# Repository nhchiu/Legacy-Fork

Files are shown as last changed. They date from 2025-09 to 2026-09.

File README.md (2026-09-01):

# Legacy Fork

*It's not only a fork of [Voron Legacy](https://github.com/VoronDesign/Voron-Legacy), but also a big "fork" (a.k.a. [Voron Trident](https://github.com/VoronDesign/Voron-Trident)).*

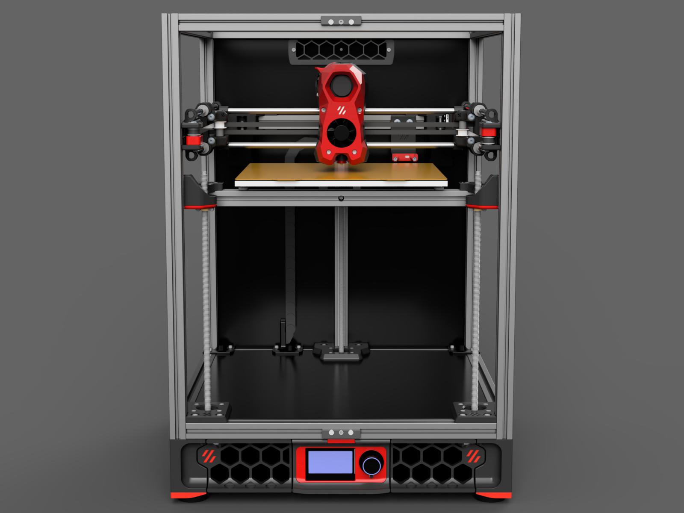
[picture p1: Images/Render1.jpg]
Render1


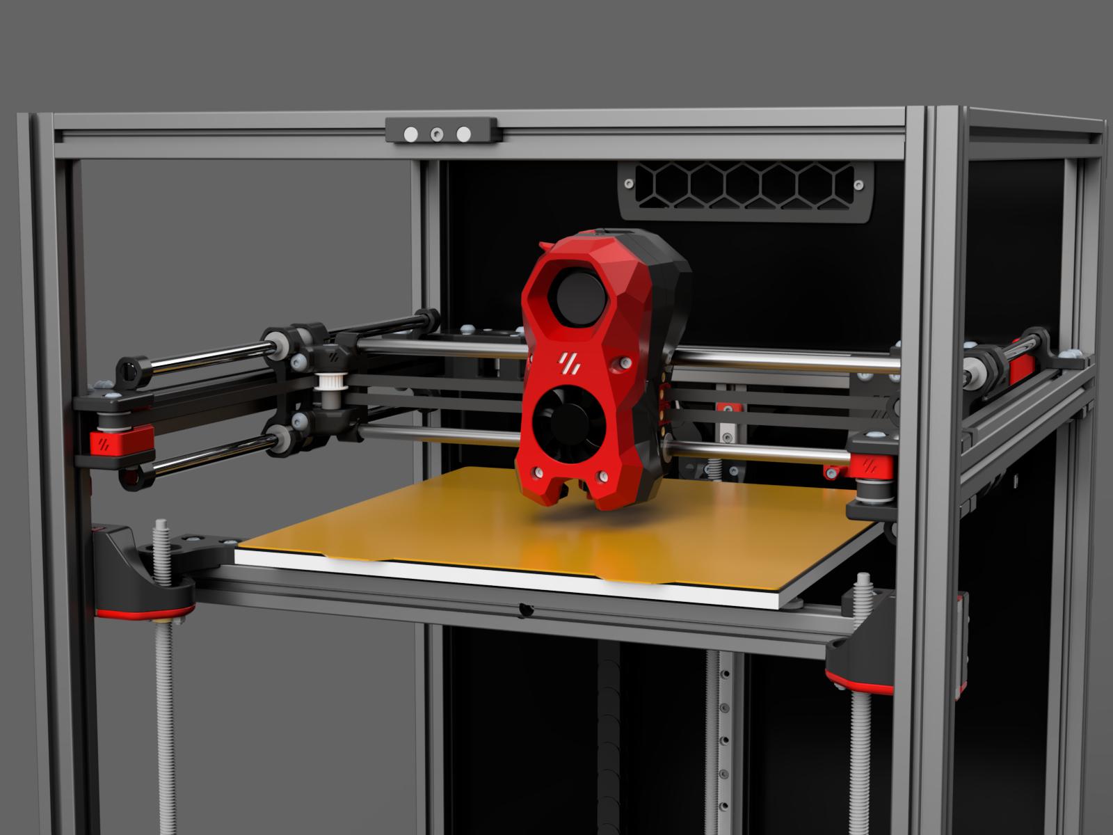
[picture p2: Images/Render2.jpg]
Render2


## Features

- Print size: 250mm x 250mm x 250mm.
- Trident 250 with Legacy style gantry.
- [Stealthburner](https://github.com/VoronDesign/Voron-Stealthburner) or [A4T](https://github.com/Armchair-Heavy-Industries/A4T) toolhead, umbilical wire management (no drag chains).
- KlickyNG for Z tilt and bed mesh.

This printer is not design for everyone.
It's just a slightly more "modernized" version of Legacy (also slightly larger print area).
If you're looking for a good reliable printer, build a Trident.

Here's a simple comparison to help you decide:

| | Legacy | Legacy Fork | Trident |
| --- | --- | --- | --- |
| Frame Size (W\*D\*H) | 410 \* 410 \* 410 | 410 \* 410 \* 500 | 410 \* 410 \* 500 |
| Print Area (X\*Y\*Z) | 230 \* 230 \* 240 | **250 \* 250 \* 250**  | **250 \* 250 \* 250** |
| Enclosure | No | **Yes** | **Yes** |
| Expected Speed/Accel | Lower | Lower | **Higher** |
| Motion system | 10 rods | 6 rods(XY), 3 rails(z) | 6 rails |

## BOM

[BOM.md](./BOM.md)

## Recommended Mods

- [PUG (Parametric umbilical gland)](https://www.printables.com/model/378567-pug-parametric-umbilical-gland)
- [Trident Inverted Electronics Bay Mod](https://github.com/VoronDesign/VoronUsers/tree/main/printer_mods/LoganFraser/TridentInvertedElectronics)
- [Print-in-place Panel Latch](https://www.printables.com/model/1042802-sturdy-print-in-place-panel-latch-for-2020-extrusi)
- [Foldable Spool holder](https://www.printables.com/model/1233299-tri-direction-foldable-spool-holder)
- [Sturdy handler](https://www.printables.com/model/793387-voron-24r2trident-sturdy-handler-remix)

## Credits

- [Voron Design](https://vorondesign.com/) team for Trident, Legacy, and Stealthburner.
- [Klicky(NG) Probe](https://github.com/jlas1/Klicky-Probe).
- [Voron Construct](https://github.com/PrintersForAnts/Voron-Construct) for handy CAD models.
- [Prusawire](https://www.printables.com/model/1363547-prusawire-2025b1-beta-1) for the belt tensioner design.
- [ApexClips](https://github.com/ApexArray/ApexClips).

> [!TIP]
> Support my work on the following platforms. Thank you!
>
> 
> 

## Changelog

### 2026 / 09 / 01

- AB drive mounts
  - Shift the assembly 2mm towards the front to fit rear panel with 1mm foam. *(untested)*
- X carriage
  - Added a variant for inductive probe (OMRON TL-Q5MC2). *(untested)*
- XY joints
  - Adjusted to fit the other changes.

### 2026 / 08 / 21

- Port Trident R2 upgrades:
  - Uses Trident R2 Z assembly.
  - New AB drive mounts:
    - Shorter belt path. (requires **4 more F695 bearings**)
    - Steppers mount with all 4 screws.
    - Cutouts for wires to pass through.
    - ~Requires **3mm foam on the rear panel**.~
- Clamping mechanism on X rod holders.
- Shifted the print area towards the front so it uses stock Trident Z carriages / bed mounts.

### 2025 / 10 / 21

Use hex nuts instead of heatset inserts to hold the X axis onto XY joints.

### 2025 / 10 / 02

New belt clip and tensioner design.

- Belt tensioner design inspired by [Prusawire](https://www.printables.com/model/1363547-prusawire-2025b1-beta-1).
- [ApexClips](https://github.com/ApexArray/ApexClips)
- Now the front idlers are fixed position.

### 2025 / 09 / 10

Initial release.

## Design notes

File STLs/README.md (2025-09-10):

The STLs regarding the following sub-assemblies are not included:

- Toolhead
- Electronics
- Exhaust Filter
- Panels
- Skirt
- Spool Management

The default is to use parts from [the Trident repository](https://github.com/VoronDesign/Voron-Trident/tree/main/STLs). Most Trident mods should be compatible.

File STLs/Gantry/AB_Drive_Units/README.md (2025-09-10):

# Flipped B drive?

It means mounting the motor on the upper side of the gantry.

Pros: The belt is closer to the motor body so there's less bending torque on the motor shaft.

Cons: Depending on how you mount the umbilical wires / cable gland, the B motor might collide to the back of the toolhead when homing.
One way to get around it is to home X axis before homing Y. There should be enough over-travel so it won't collide in the print area.

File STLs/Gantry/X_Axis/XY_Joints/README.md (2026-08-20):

Put one of the `Printed_Shim_0.7mm` at both sides of the 20T idlers if you're using generic/POWGE ones (about 8.5mm width), so the total width adds up to 10mm.

Check the width of your idler to see if you need it (e.g. Gates idler).

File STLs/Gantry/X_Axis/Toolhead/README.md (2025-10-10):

# Toolhead

- [Voron Stealthburner](https://github.com/VoronDesign/Voron-Stealthburner/tree/main/STLs)
- [A4T](https://github.com/Armchair-Heavy-Industries/A4T) (CW2 carriage)

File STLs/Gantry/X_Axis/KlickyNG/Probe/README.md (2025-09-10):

Get the STLs from here: [https://github.com/jlas1/Klicky-Probe/blob/main/Probes/KlickyNG/STL/KlickyNG_Probe.zip](https://github.com/jlas1/Klicky-Probe/blob/main/Probes/KlickyNG/STL/KlickyNG_Probe.zip).

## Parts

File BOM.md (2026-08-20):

# BOM

This is a very brief BOM. Only core components are listed here.
Refer to CAD, Trident and Legacy BOM for the rest.

> [!NOTE]
> \* Aliexpress links are *affiliate links*. If you purchase products through these links,
> I may earn a small commission at no additional cost to you.
> This helps support the development and maintenance of my projects.

## Trident 250 Components

| Component | Qty | Source |
| --- | --- | --- |
| Frame kit | 1 | [West3D](https://west3d.com/products/ldo-trident-frame-kit-multiple-colors) or [KB3D](https://kb-3d.com/store/frame-enclosure/471-8401-ldo-motors-frame-kit-for-voron-trident-multiple-types-1642791073246.html) |
| Panels | 1 | |
| Build plate + Heater | 1 | [West3D (LDO)](https://west3d.com/products/voron-v2-4-aluminum-build-plate-complete-kit-by-ldo-systems-heater-magnet-and-fuse-pre-applied-to-plate) |

## Fasteners

| Component | Qty | Notes | Source |
| --- | --- | --- | --- |
| M5 0.5mm Thick Shim/Washer | 20  | Optional. For alternative bearing stacks (check manual) | [Aliexpress\*](https://s.click.aliexpress.com/e/_c4MMENC7) - 5x10x0.5mm |

## Motion

| Component | Qty | Notes | Source |
| --- | --- | --- | --- |
| Linear Rods - D8mm x 320mm | 6 | | [CNA\*](https://s.click.aliexpress.com/e/_c4bX2dSv) |
| Linear Bearings - LM8LUU | 6 | | [FUSHI\*](https://s.click.aliexpress.com/e/_onqjz99)  |
| Integrated Lead Screw/Stepper Motors - 300mm | 3 | | [Siboor\*](https://s.click.aliexpress.com/e/_ombbGBv) |
| Linear Rail - MGN9H 300mm | 3 | | [CNA\*](https://s.click.aliexpress.com/e/_onEsgxV) |
| GE5C Spherical Bearing | 3 | | [FUSHI\*](https://s.click.aliexpress.com/e/_olhEbNN)  |
| GT2 20T (6mm wide) Pulley (5mm bore) | 3 | 1 is for Z endstop | [POWGE\*](https://s.click.aliexpress.com/e/_oEvDEoR)  |
| GT2 20T (6mm wide) Toothed Idler (5mm bore)  | 2 | | [POWGE\*](https://s.click.aliexpress.com/e/_olP1HSr)  |
| GT2 Open Belt LL-2GT-RF (6mm wide) | 5m  | Only need roughly 3.2m | [POWGE\*](https://s.click.aliexpress.com/e/_olP1HSr)  |
| F695 Bearing | 24  | | [FUSHI\*](https://s.click.aliexpress.com/e/_oo38KNh)  |
| NEMA17 Motors | 2 | AB motor | [Mellow\*](https://s.click.aliexpress.com/e/_om0OSnH) |

## Electronics

| Component | Qty | Notes |
| --- | --- | --- |
| Mouse Button - Micro Switch | 4 | X, Y, Z, Probe |
| SBC (Raspberry Pi alternatives) | 1 | |
| Controllers / Toolhead boards | 1 | 6 steppers in total |

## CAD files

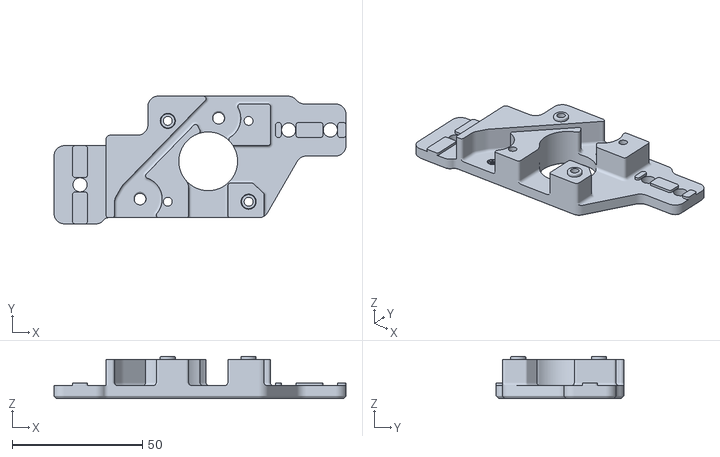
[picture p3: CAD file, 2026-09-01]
STLs/Gantry/AB_Drive_Units/B_Drive_a.stl
112.0 x 49.0 x 16.2

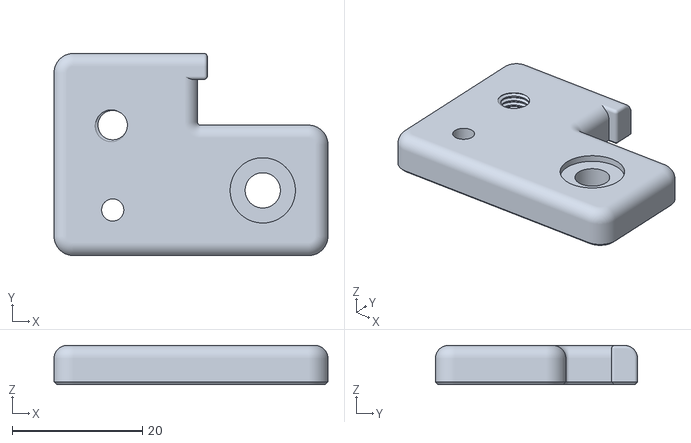
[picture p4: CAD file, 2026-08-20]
STLs/Gantry/Front_Idlers/Right_b.stl
42.0 x 31.0 x 6.00

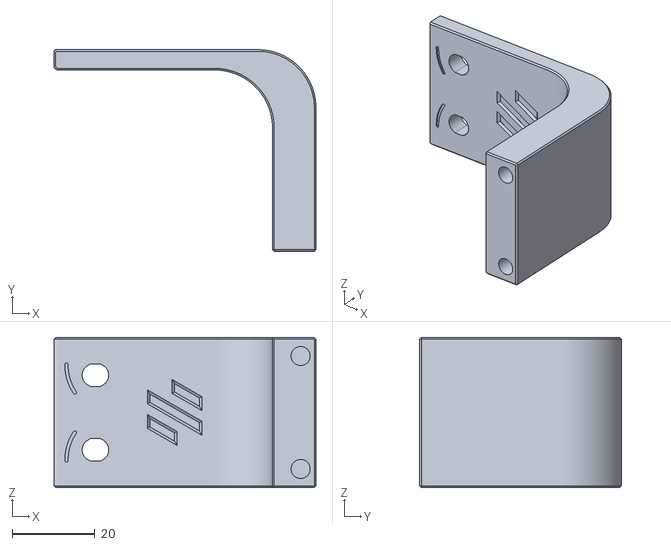
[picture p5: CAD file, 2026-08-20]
STLs/Gantry/X_Axis/KlickyNG/Dock/Dock_Mount.stl
63.2 x 48.7 x 36.3

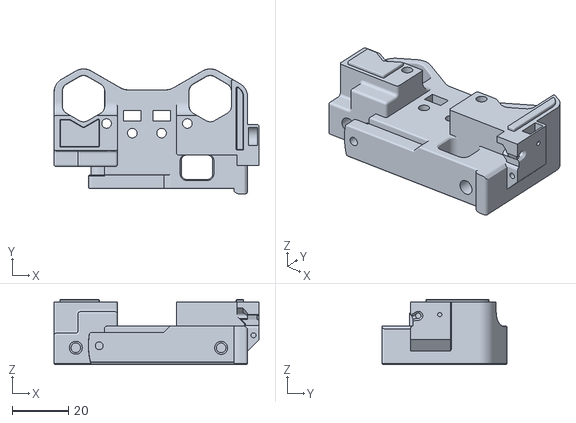
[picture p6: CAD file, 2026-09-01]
STLs/Gantry/X_Axis/X_Carriage/x_carriage_frame_left_klickyNG.stl
72.8 x 44.5 x 23.2

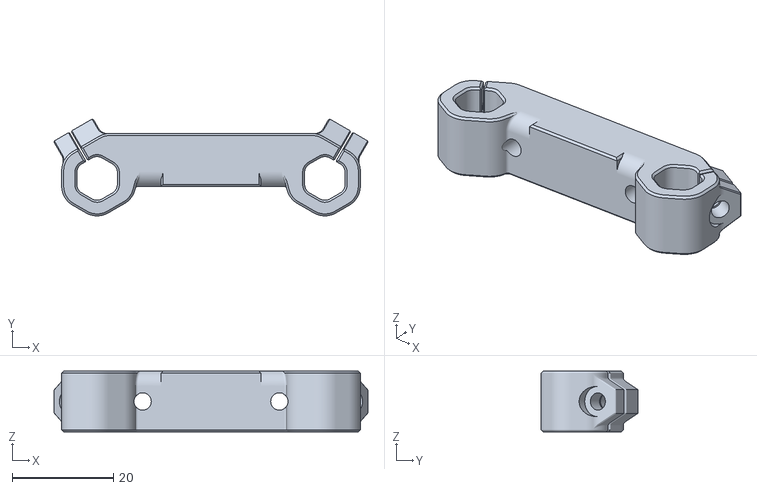
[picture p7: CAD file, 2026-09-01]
STLs/Gantry/X_Axis/XY_Joints/X_Back_Brace_x2.stl
62.0 x 19.1 x 12.0

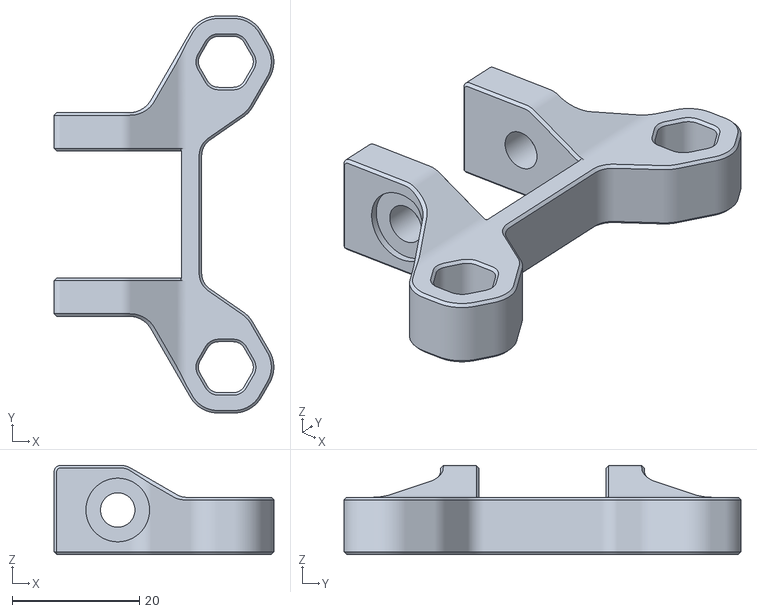
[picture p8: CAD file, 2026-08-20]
STLs/Gantry/Y_Shaft_Holder_x4.stl
34.5 x 62.4 x 14.0

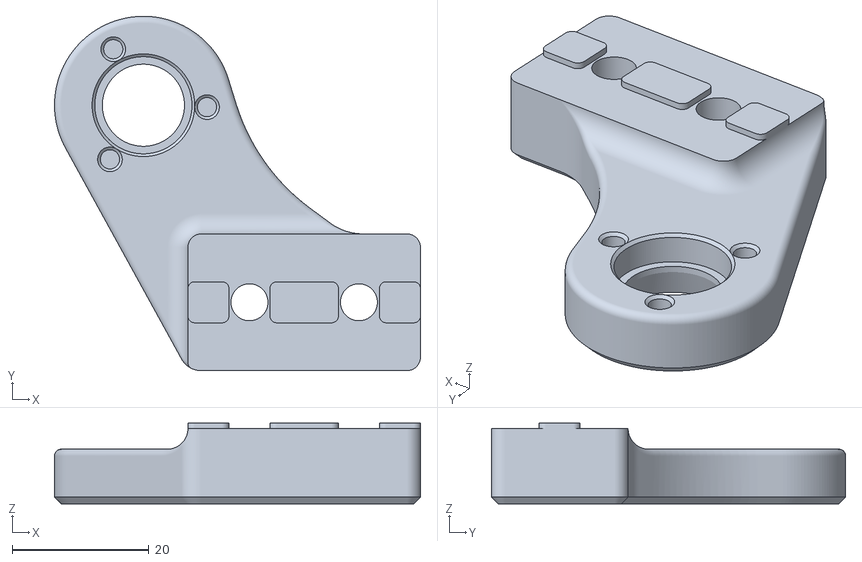
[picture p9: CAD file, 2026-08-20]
STLs/Z_Assembly/Z_Bed_Left.stl
53.5 x 51.8 x 11.8

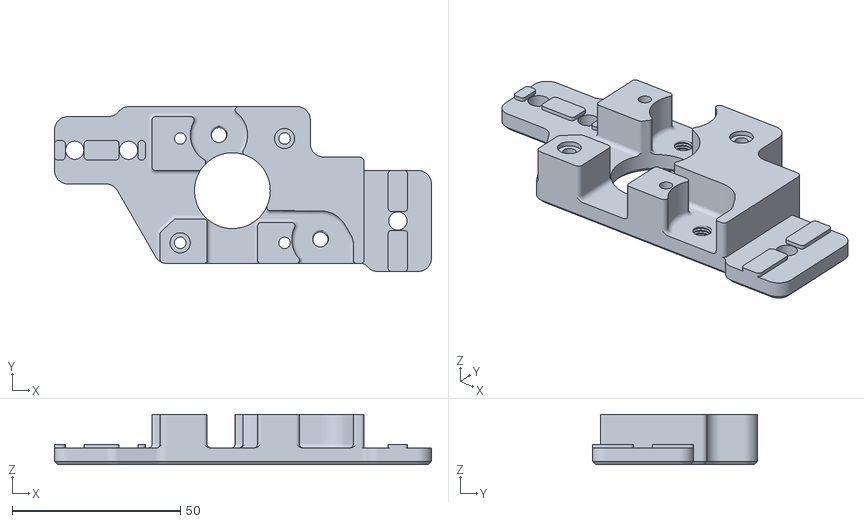
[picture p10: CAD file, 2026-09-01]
STLs/Gantry/AB_Drive_Units/A_Drive_a.stl
112.0 x 49.0 x 15.0

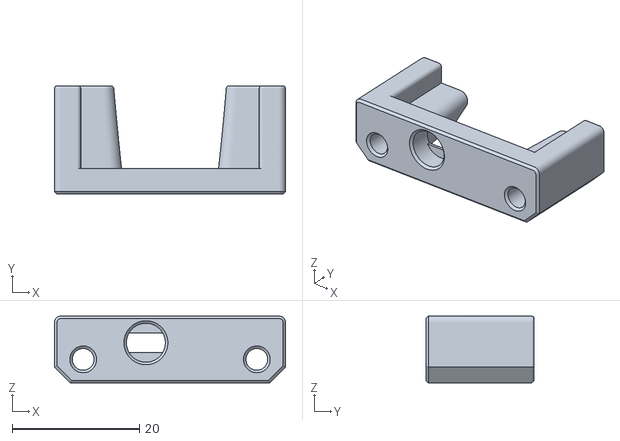
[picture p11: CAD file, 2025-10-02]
STLs/Gantry/X_Axis/KlickyNG/Dock/[a]_Probe_Dock.stl
36.3 x 17.0 x 10.5

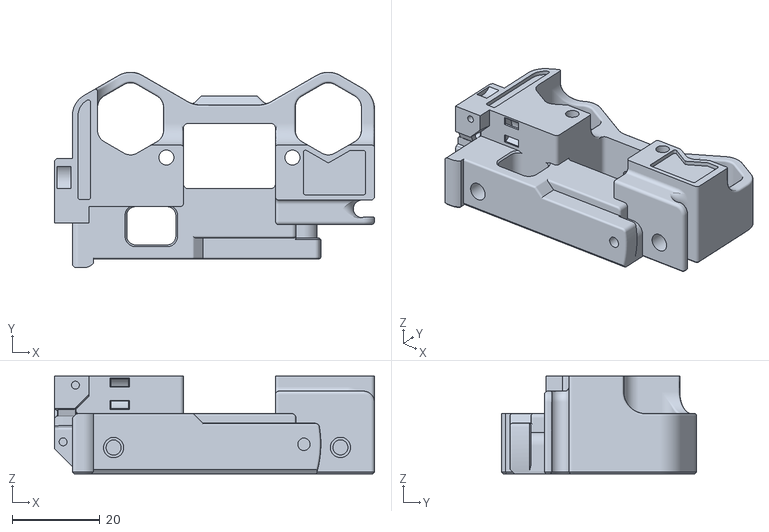
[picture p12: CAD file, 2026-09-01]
STLs/Gantry/X_Axis/X_Carriage/x_carriage_frame_right_klickyNG.stl
72.8 x 44.5 x 22.2

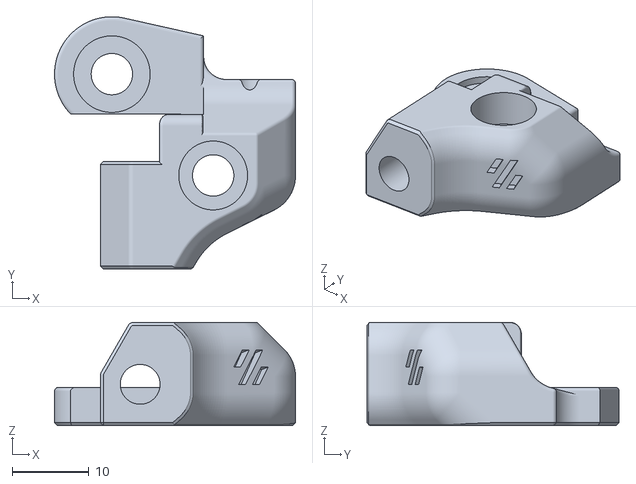
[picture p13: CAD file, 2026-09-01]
STLs/Gantry/X_Axis/XY_Joints/XY_Joint_Left_a.stl
31.5 x 33.0 x 13.5

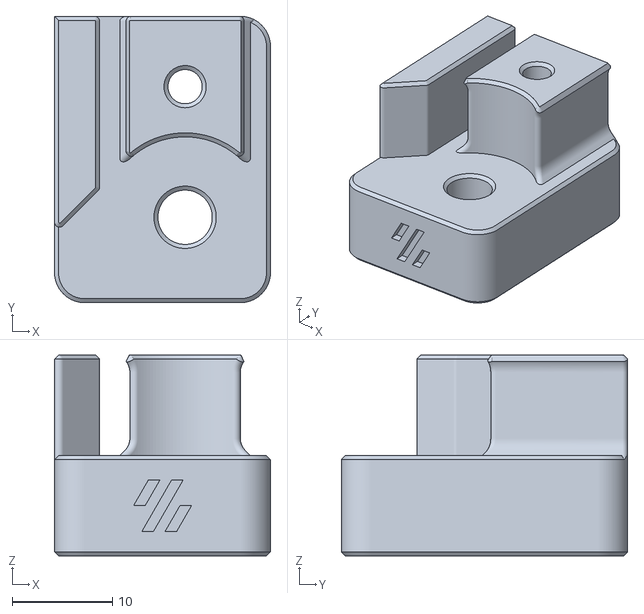
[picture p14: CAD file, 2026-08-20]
STLs/Gantry/Front_Idlers/[a]_Tensioner_x2.stl
21.5 x 28.5 x 20.0

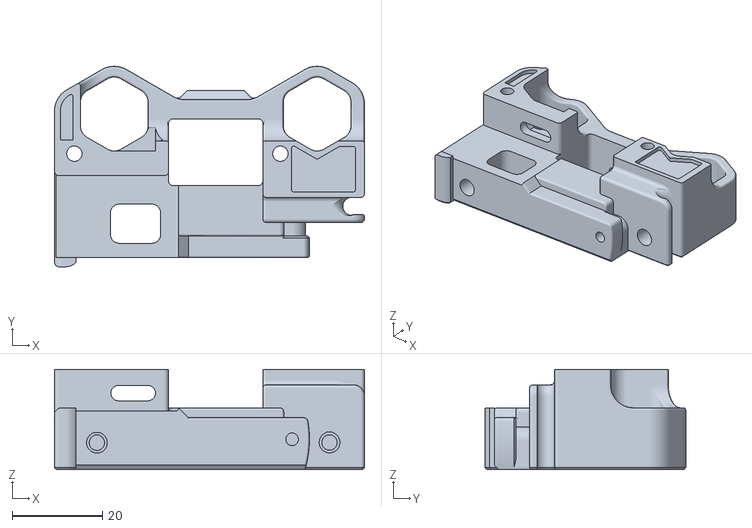
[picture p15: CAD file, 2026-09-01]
STLs/Gantry/X_Axis/X_Carriage/x_carriage_frame_right_inductive.stl
68.8 x 44.5 x 22.2

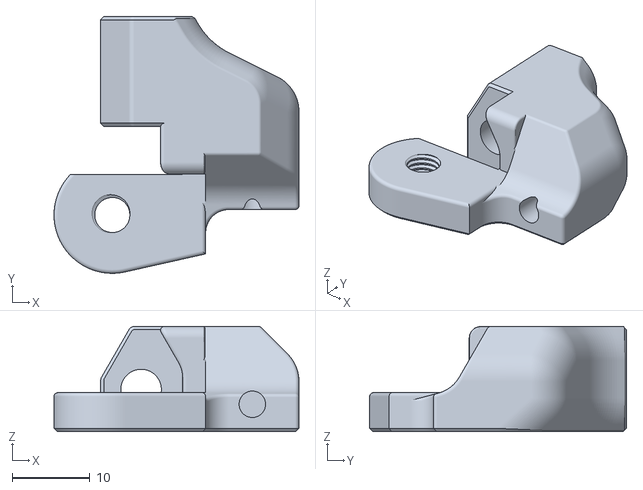
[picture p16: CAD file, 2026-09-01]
STLs/Gantry/X_Axis/XY_Joints/XY_Joint_Left_b.stl
31.5 x 33.0 x 13.5

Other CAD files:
STLs/Gantry/Front_Idlers/Left_a.stl
STLs/Z_Assembly/Z_Bed_Right.stl
STLs/Gantry/AB_Drive_Units/B_Drive_Flipped_b.stl
STLs/Z_Assembly/Z_Bed_Rear.stl
STLs/Gantry/AB_Drive_Units/A_Drive_b.stl
STLs/Gantry/AB_Drive_Units/B_Drive_Flipped_a.stl
STLs/Gantry/AB_Drive_Units/B_Drive_b.stl
STLs/Gantry/AB_Drive_Units/[a]_cover_logo_x2.stl
STLs/Gantry/Front_Idlers/Left_b.stl
STLs/Gantry/Front_Idlers/Right_a.stl
STLs/Gantry/X_Axis/XY_Joints/Printed_Shim_0.7mm_x4.stl
STLs/Gantry/X_Axis/XY_Joints/XY_Joint_Right_a.stl
STLs/Gantry/X_Axis/XY_Joints/XY_Joint_Right_b.stl
STLs/Gantry/X_Axis/XY_Joints/Y_Bearing_Retainer_front_x2.stl
STLs/Gantry/X_Axis/XY_Joints/Y_Bearing_Retainer_rear_x2.stl
STLs/Gantry/X_Axis/XY_Joints/[a]_Idler_Spacer_x4.stl
STLs/Gantry/X_Axis/X_Carriage/[a]_belt_clip_x4.stl
STLs/Gantry/X_Axis/X_Carriage/[a]_belt_tensioner_x2.stl
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

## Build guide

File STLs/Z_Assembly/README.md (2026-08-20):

Get the full Z assembly from Trident's repo.
These bed mounts raise the bed by 2mm.
Use them if the nozzle still can't reach the bed when the Z carriages are raised to the top.

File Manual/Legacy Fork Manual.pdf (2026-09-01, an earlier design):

# LEGACY FORK MANUAL

It's not only a fork of Voron Legacy, but also a big "fork" (a.k.a. Voron Trident).

VERSION 2026-09-01

### TABLE OF CONTENTS

2

A/B DRIVE & IDLER | 04
X AXIS | 17
BELTS | 33

2

Follow the official Voron Trident manual
Most of the printer is assembled as a Voron Trident.
Come back to this manual for the gantry sub-assemblies (A/B drives, idles, XY axis, and belts).

### A/B DRIVE & IDLER

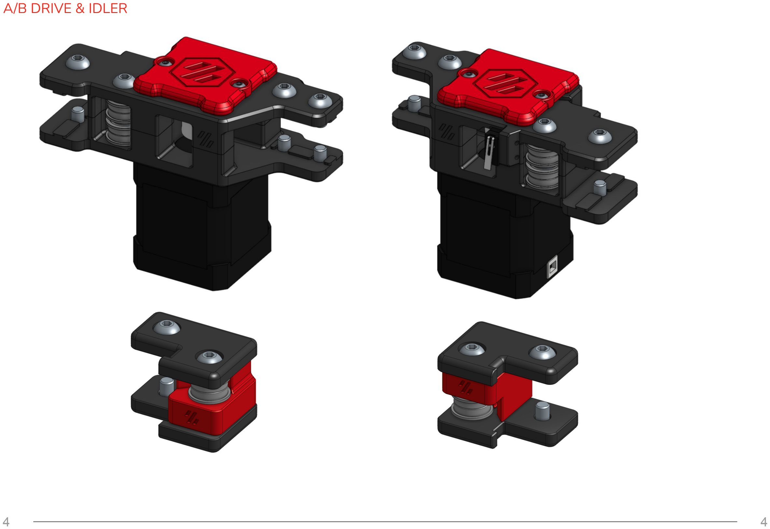
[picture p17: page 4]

Stock bearing stack | Alternative bearing stack

### Bearing Stacks

F695 bearing stacks
There are two ways to build a bearing stack. The alternative stack has a small clearance for the belt and thus less likely to wear out, but it requires additional hardware (M5x0.5mm shims) from the stock BOM.
The components are listed from top to bottom:
1. The stock bearing stack: M5 1mm shim - F695 (flange up) - F695 (flange down) - M5 1mm shim
2. Alternative bearing stack: M5 0.5mm shim - F695 (flange up) - M5 1mm shim - F695 (flange down) - M5 0.5mm shim

M5x1mm Shim

F695 Bearing

F695 Bearing

F695 Bearing

F695 Bearing

M5x1mm Shim

M5x1mm Shim

M5x0.5mm Shim

M5x0.5mm Shim

Don’t over-tighten and strip the thread!

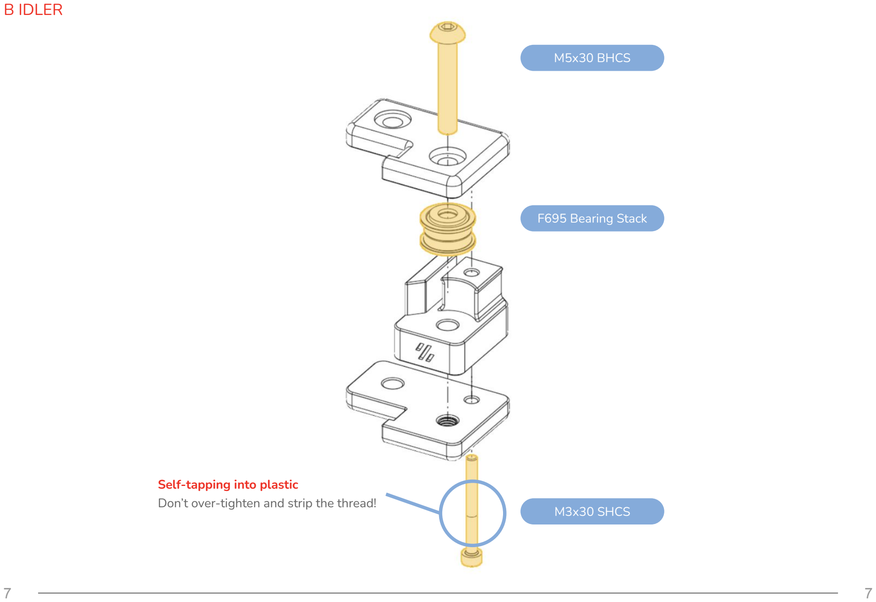
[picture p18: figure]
B IDLER; M5x30 BHCS; F695 Bearing Stack; M3x30 SHCS; Self-tapping into plastic

Don’t over-tighten and strip the thread!

### A/B IDLER

M5x10 BHCS

B IDLER | A IDLER

For reference only. Use these to attach to the frame.

### A DRIVE

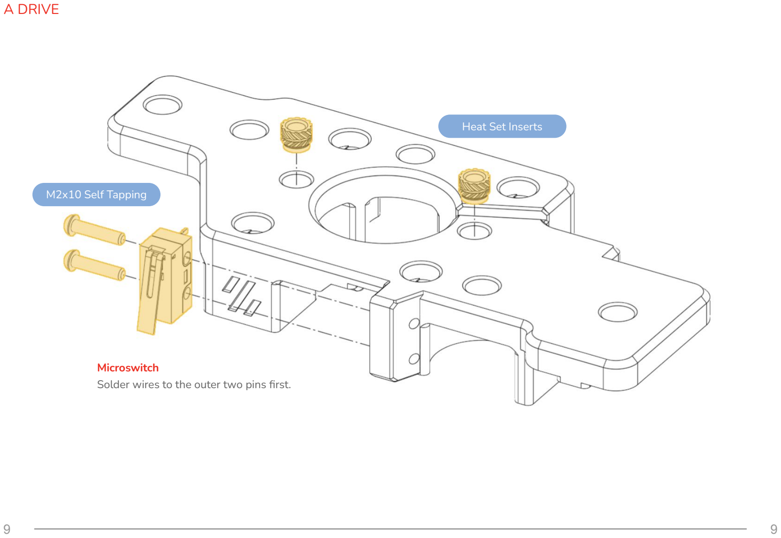
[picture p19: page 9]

Microswitch
Solder wires to the outer two pins first.

M2x10 Self Tapping

Heat Set Inserts

### A DRIVE

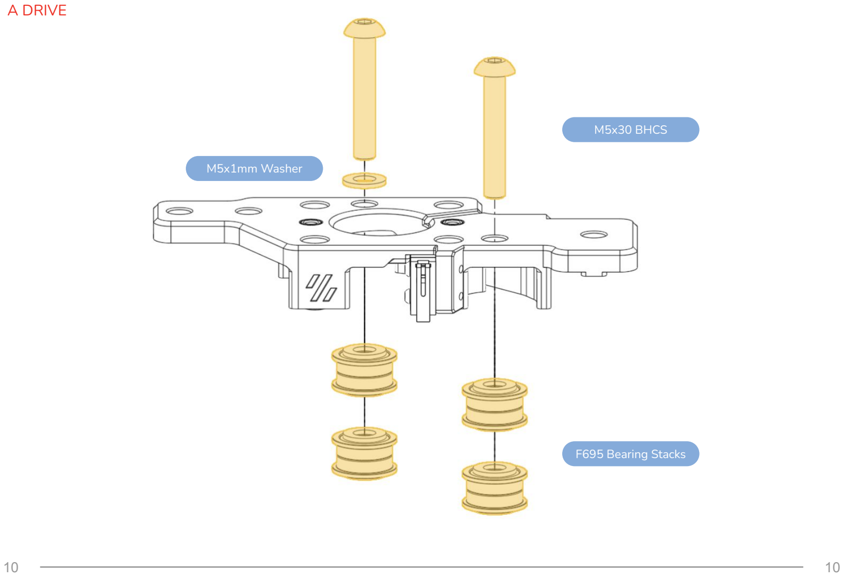
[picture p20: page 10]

M5x30 BHCS

F695 Bearing Stacks

M5x1mm Washer

### A DRIVE

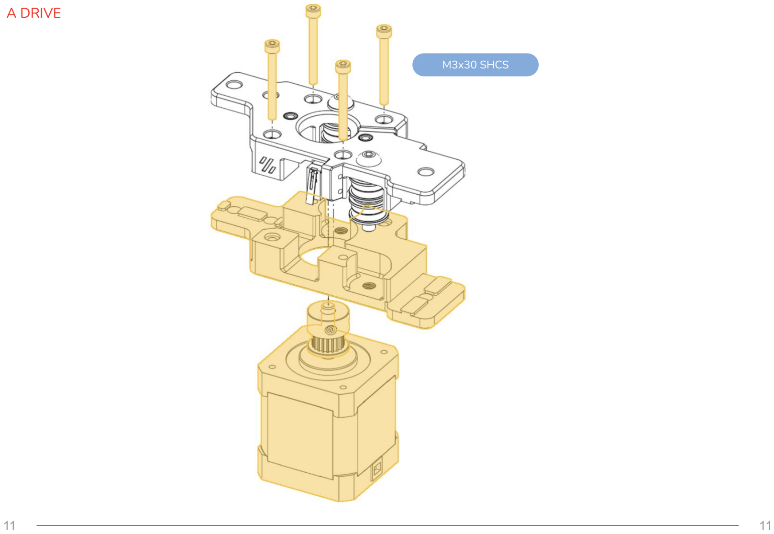
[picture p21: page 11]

M3x30 SHCS

### A DRIVE

M3x6 BHCS

Y endstop wires
The wires from the microswitch go through this slot.

### A DRIVE

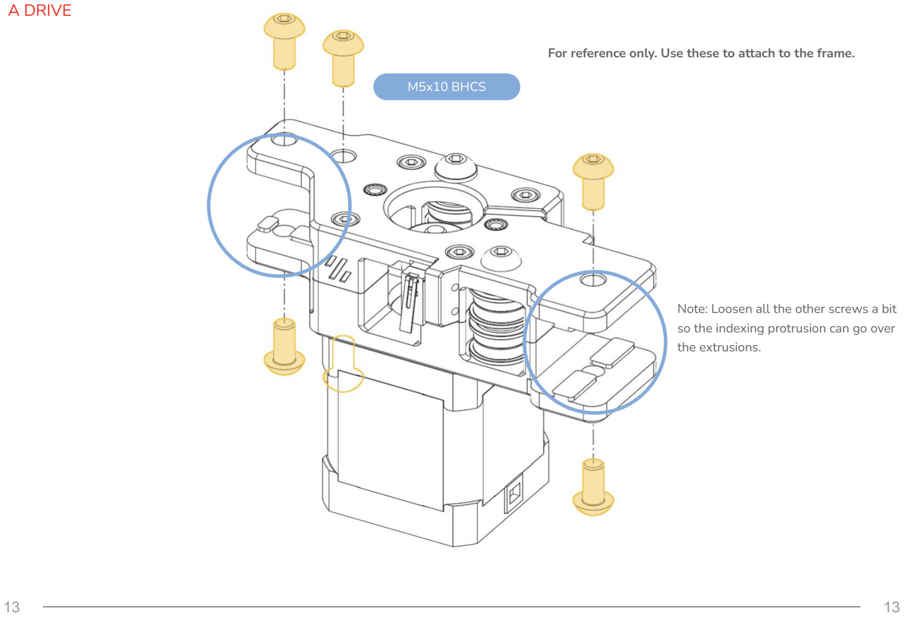
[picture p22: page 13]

M5x10 BHCS

For reference only. Use these to attach to the frame.

Note: Loosen all the other screws a bit so the indexing protrusion can go over the extrusions.

### B DRIVE

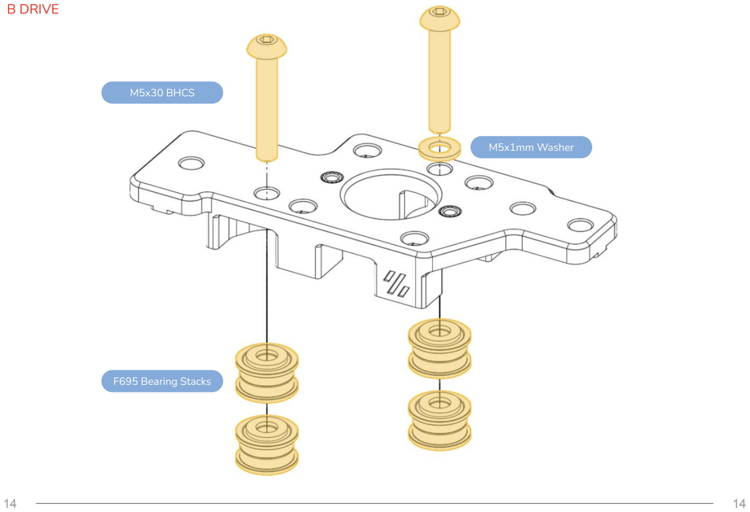
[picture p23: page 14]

M5x30 BHCS

F695 Bearing Stacks

M5x1mm Washer

### B DRIVE

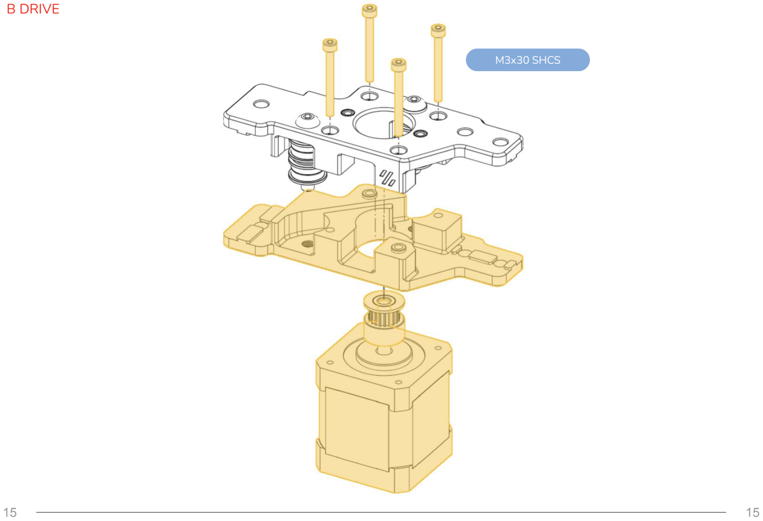
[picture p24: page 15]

M3x30 SHCS

### B DRIVE

M3x6 BHCS

### B DRIVE

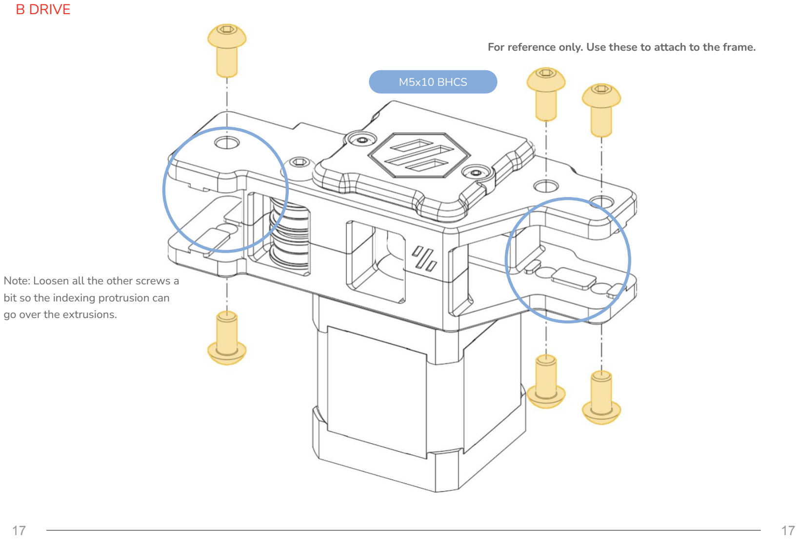
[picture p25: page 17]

M5x10 BHCS

Note: Loosen all the other screws a bit so the indexing protrusion can go over the extrusions.

For reference only. Use these to attach to the frame.

### X AXIS

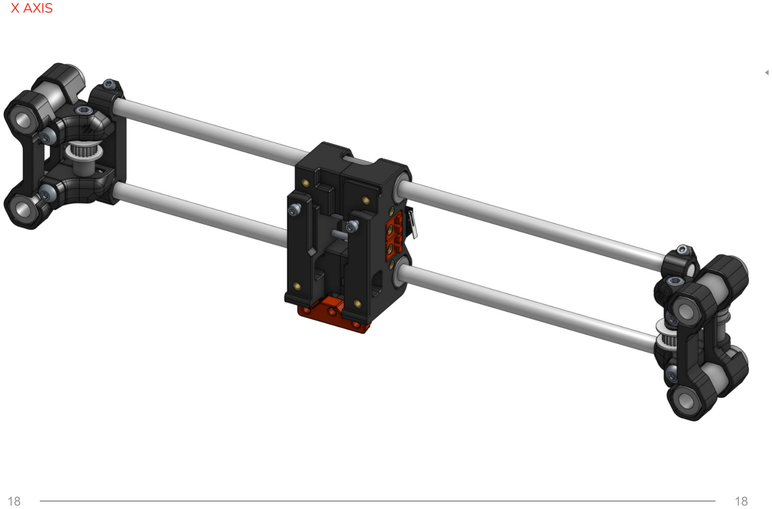
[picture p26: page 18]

### LEFT XY JOINT

M3 Nut

### LEFT XY JOINT

M5x40 SHCS

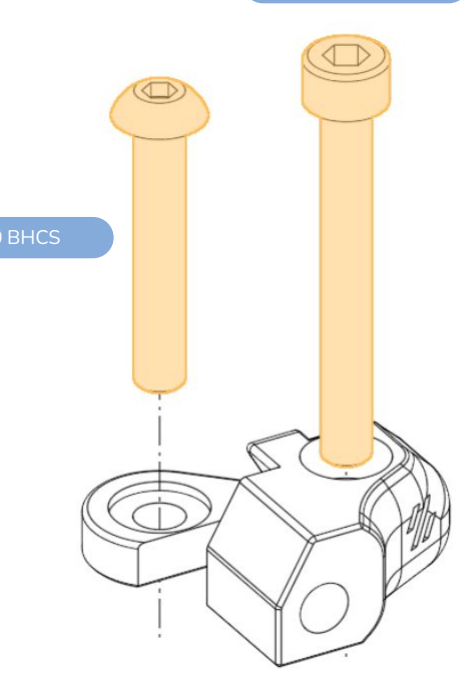
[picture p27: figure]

M5x30 BHCS

### LEFT XY JOINT

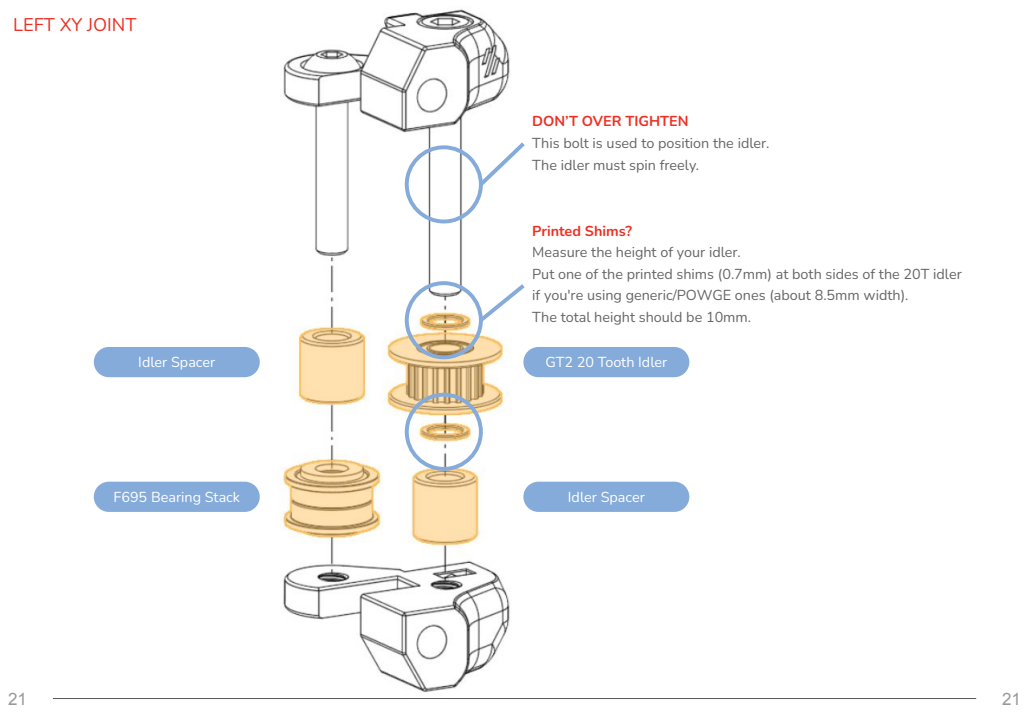
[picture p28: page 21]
Idler Spacer; F695 Bearing Stack; GT2 20 Tooth Idler

DON’T OVER TIGHTEN
This bolt is used to position the idler.
The idler must spin freely.

Printed Shims?
Measure the height of your idler.
Put one of the printed shims (0.7mm) at both sides of the 20T idler
if you're using generic/POWGE ones (about 8.5mm width).
The total height should be 10mm.

### LEFT XY JOINT

M5 Nuts

Y_Bearing_Retainer_Rear

### LEFT XY JOINT

M5x25 BHCS

Y_Bearing_Retainer_Rear

Y_Bearing_Retainer_Front

### LEFT XY JOINT

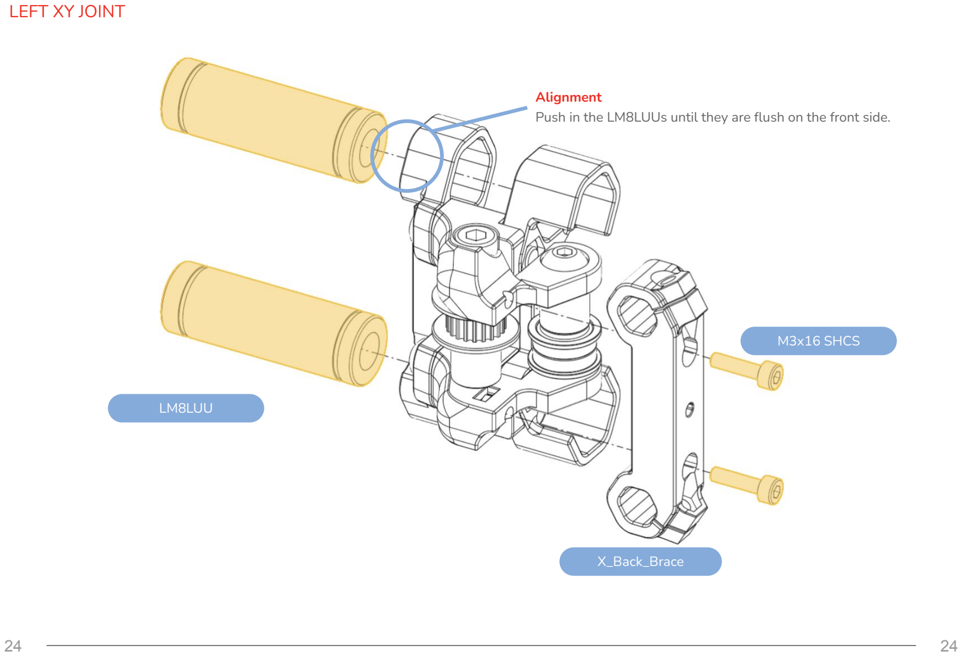
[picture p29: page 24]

M3x16 SHCS

X_Back_Brace

LM8LUU

Alignment
Push in the LM8LUUs until they are flush on the front side.

### LEFT XY JOINT

M3x12 SHCS

M3 Nut

### RIGHT XY JOINT

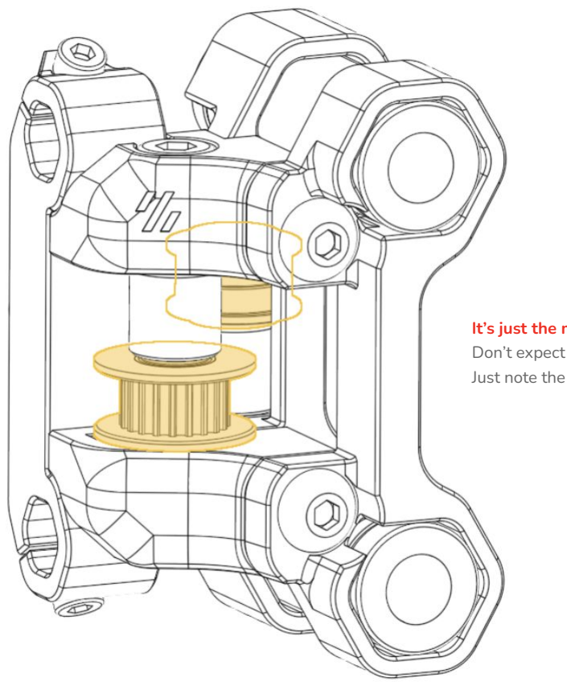
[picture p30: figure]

It’s just the mirror of the left side Don’t expect too much from this manual. Just note the placement of the idlers.

### RIGHT XY JOINT

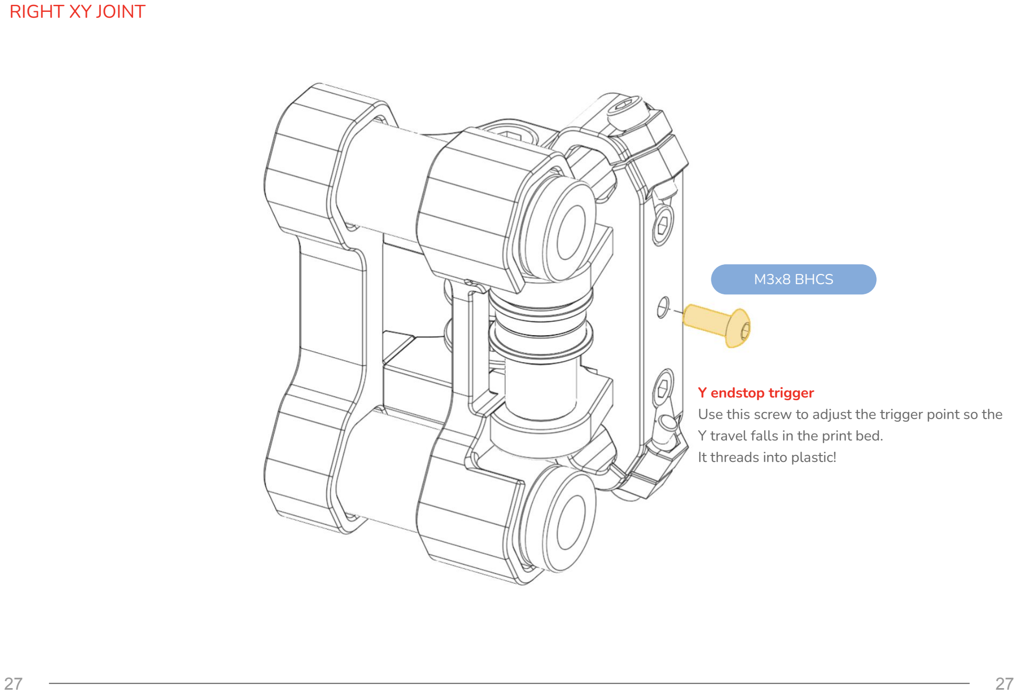
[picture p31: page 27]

Y endstop trigger
Use this screw to adjust the trigger point so the Y travel falls in the print bed.
It threads into plastic!

M3x8 BHCS

### X CARRIAGE

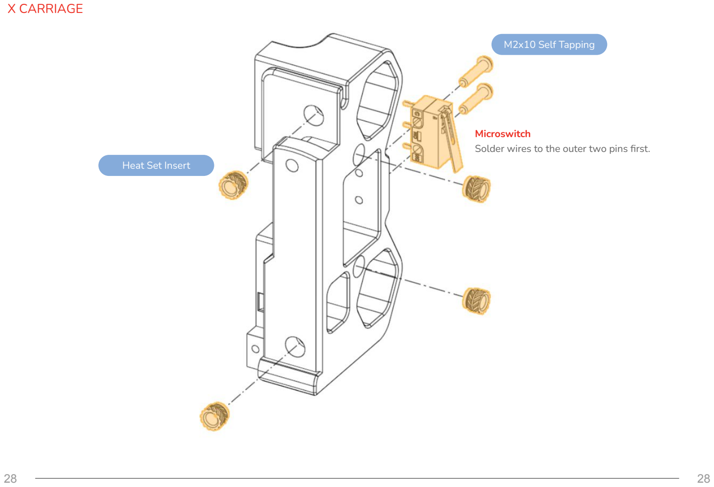
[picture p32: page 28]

Microswitch
Solder wires to the outer two pins first. Heat Set Insert

M2x10 Self Tapping

### X CARRIAGE

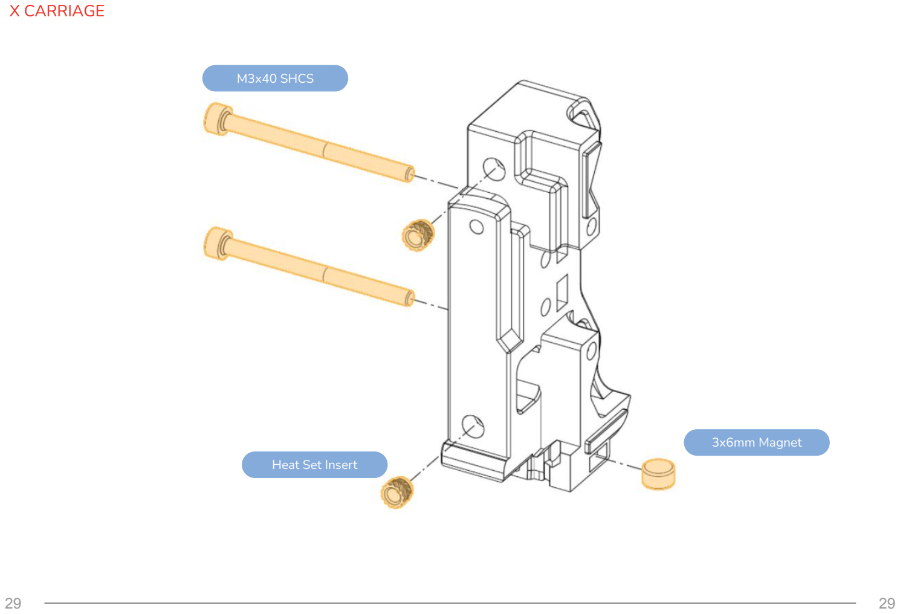
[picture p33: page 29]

Heat Set Insert

M3x40 SHCS

3x6mm Magnet

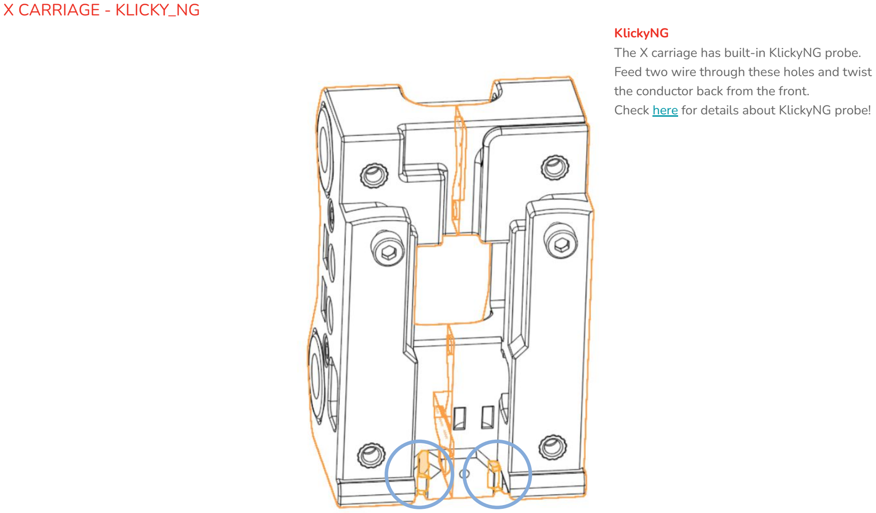
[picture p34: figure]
X CARRIAGE - KLICKY_NG; KlickyNG; the conductor back from the front.

The X carriage has built-in KlickyNG probe. Feed two wire through these holes and twist

Check here (https://github.com/jlas1/Klicky-Probe/tree/main/Probes/KlickyNG) for details about KlickyNG probe!

### X CARRIAGE - KLICKY_NG

Mind the polarity
These two magnets have the same direction of polarity, and should be opposite to the previously installed one.

M2x10 Self Tapping

3x6mm Magnet

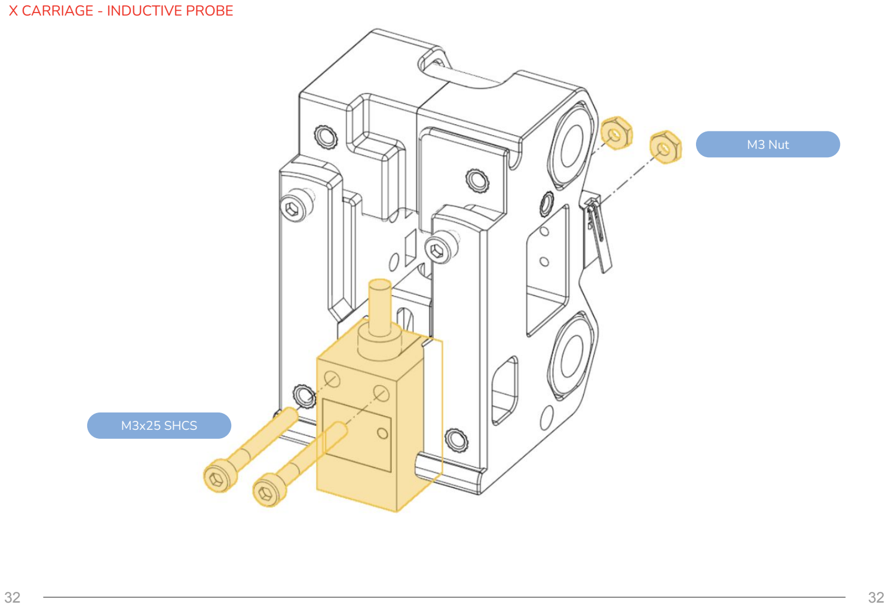
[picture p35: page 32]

X CARRIAGE - INDUCTIVE PROBE

M3x25 SHCS

M3 Nut

### X CARRIAGE

LM8LUU

M3x12 SHCS

Leave a gap of about 3mm

### X CARRIAGE

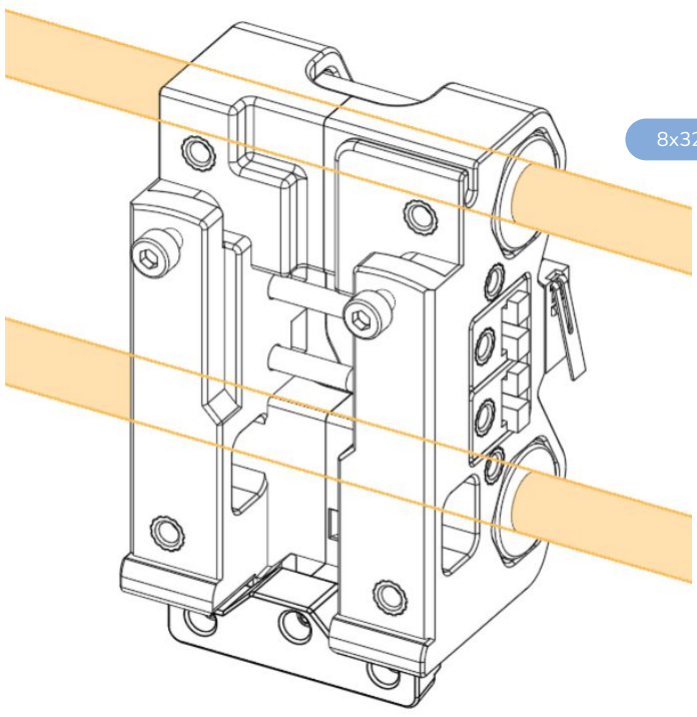
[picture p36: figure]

8x320mm Linear Rods

### X CARRIAGE

### BELTS

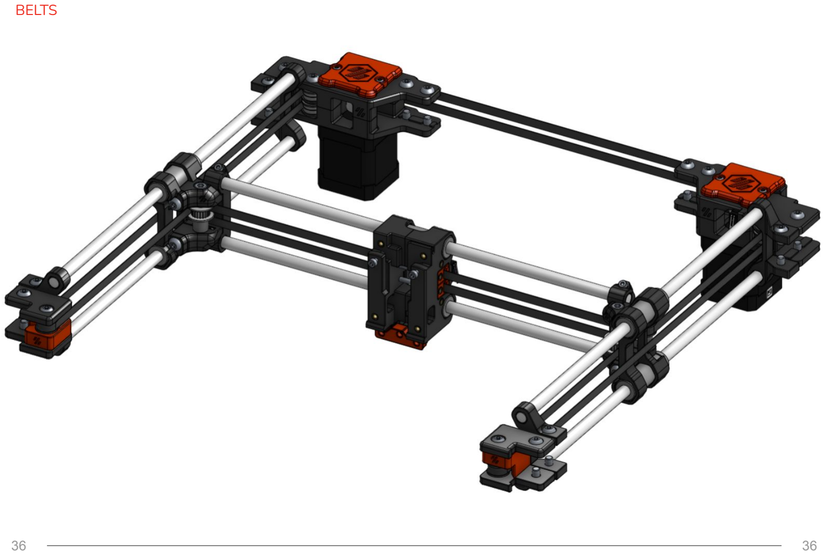
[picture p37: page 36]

### Y AXIS

8x320mm Linear Rods

M5x10 BHCS

### BELTS

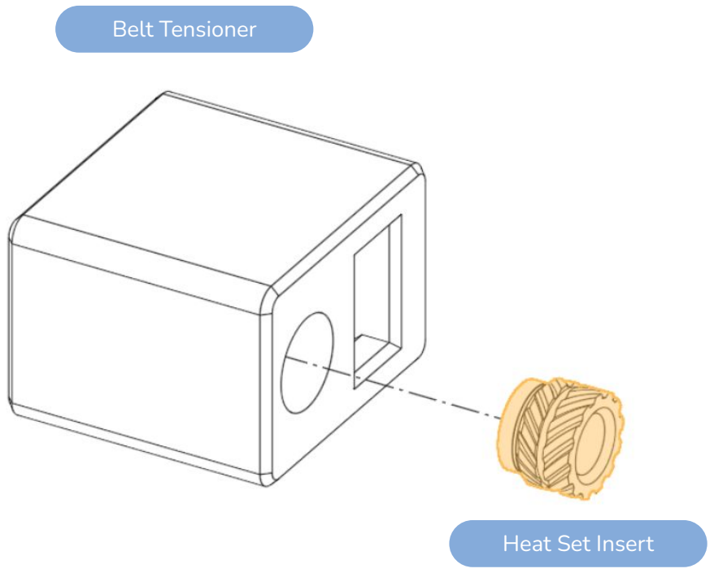
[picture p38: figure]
Belt Tensioner; Heat Set Insert

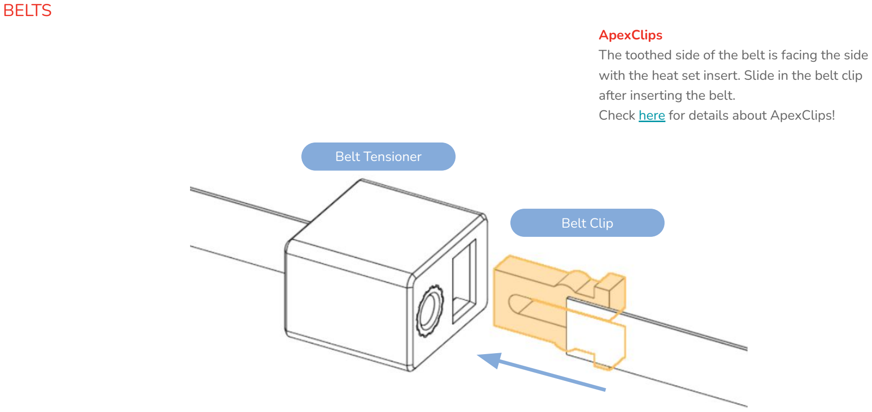
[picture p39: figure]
BELTS; Belt Tensioner; Belt Clip; ApexClips; after inserting the belt. Check here for details about ApexClips!

The toothed side of the belt is facing the side with the heat set insert. Slide in the belt clip

### BELTS

Rout the belts
Feed the belts through the whole gantry and clip the other end of the belts to the X carriage.

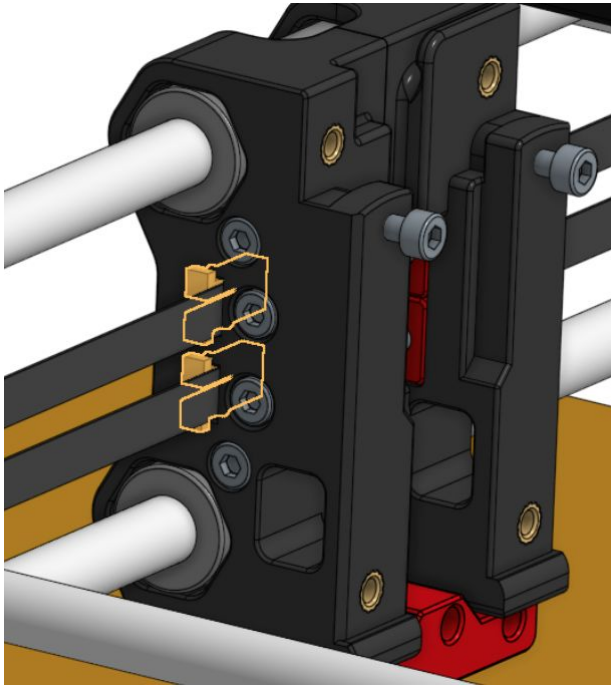
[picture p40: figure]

### BELTS

Belt Tensioners

M3x40 SHCS

GITHUB
https://github.com/nhchiu/Legacy-Fork

CONGRATULATIONS!
Now you can finish the build following the Voron Trident manual!

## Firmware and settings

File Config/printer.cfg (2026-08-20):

## This file contains only critical configuration parameters for
## Legacy Fork. Please replace/merge this file with the stock
## Trident printer.cfg file.

#####################################################################
#   Probe
#####################################################################

[probe]
# Or [dockable_probe] if you are using kalico

x_offset: -1
y_offset: 24
z_offset: 7

#####################################################################
#   Homing and Gantry Adjustment Routines
#####################################################################

[z_tilt]

z_positions:
  -50, 14
  125, 295.5
  300, 14

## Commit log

2025-09-10 Upload most files
    [Dock_Mount.stl, Front_Face_x2.stl, Left_a.stl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]
2025-09-10 Update BOM and README
2025-09-11 Update BOM
2025-10-02 New belt clip and tensioner design
    [Dock_Mount.stl, Front_Face_x2.stl, Left_a.stl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]
2025-10-10 Add A4T as compatible toolhead
2025-10-18 Update BOM sourcing links
2025-10-21 Use hex nuts to hold the X axis onto XY joints
    [XY_Joint_Left_a.stl, XY_Joint_Left_b.stl, XY_Joint_Right_a.stl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]
2025-11-14 Update link in BOM.md
2026-01-11 Add alternative F695 bearing stack to the manual
2026-01-11 Add klipper config file
    [printer.cfg]
2026-01-23 Add optional docakble_probe comment
    [printer.cfg]
